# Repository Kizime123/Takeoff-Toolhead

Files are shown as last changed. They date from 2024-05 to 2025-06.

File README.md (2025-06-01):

# Takeoff-Toolhead-Clamps
Is it about time to *takeoff* your current toolhead? Well you're in the right spot!

The **ONLY** fully open source SLM voron toolhead

An SLM toolhead using 3628s and [Chube](https://chubehotend.com), with no X loss. There will be some Y loss (17mm~ from hitting the front door) unless you have a [clicky clacky door](https://github.com/tanaes/whopping_Voron_mods/tree/main/clickyclacky_door), a v2.4 that allows moving the bed back, or a 4040-based frame, such as DoomCube

> [!WARNING]  
> For tridents, you need to cut the front left and rear leadscrew, or use [these](https://www.printables.com/model/486638-voron-trident-z-steppers-spacers) (recommended), to avoid losing travel

> [!WARNING]  
> For those aiming for high belt tensions, a pretension tool is necessary since the mount uses clamping. I recommend using [this one](https://www.printables.com/model/1027579-sovol-sv08-belt-helper-for-x-carriage).

## Luke's Laboratory is [selling kits for takeoff!](https://lukeslabonline.com/products/takeoff-toolhead) I'll be getting a percentage of each sale. If you don't wanna wait/want to support me purchase from them!

## 3Dkatten is [selling kits for takeoff!](https://3dkatten.se/en/products/takeoff-toolhead) I'll be getting a percentage of each sale. If you don't wanna wait/want to support me purchase from them!

## Klipper Setup https://github.com/KalicoCrew/kalico Kalico is the recommendation for MPC

```
[beacon]
x_offset:-23.48

[fan] #only 2 wires
max_power: 1 #set to .8 for kraken (btt moment)
off_below: 0.13

[verify_heater extruder] #use with mpc
max_error: 120
check_gain_time: 25
hysteresis: 10

[extruder]
control = mpc
heater_power: 120
#ambient_temp_sensor: temperature_fan chamber #if you have a chamber thermistor
cooling_fan: fan
#Recommend 9 minimum FAN_BREAKPOINT for calibration

#Example MPC config from Ericzimmerman
# block_heat_capacity: 26.1100
# sensor_responsiveness: 0.115066
# ambient_transfer: 0.0708064
# fan_ambient_transfer: 0.0708064, 0.147823, 0.179016, 0.19074, 0.206899, 0.22524, 0.21861
```

## Extruders Compatiblity

<u>Option A Has mounts for:</u>

LGX Lite Pro

Vz-Hextrudort

Sherpa Mini (No K-face)

Sherpa Micro (With K-face), Mellow CNC Sherpa Micro supported, but no K-face is available

Orbiter 2/Peopoly Lancer Orbiter 2 Version

<u>Option B Has mounts for: </u>

Sherpa Mini (with K-face), Fysetc CNC Sherpa Mini supported 

Peopoly Lancer new/old (rotated COM for both)

DFA/Orbital Ascender (PENDING OA RELEASE)

A3DP FXD 

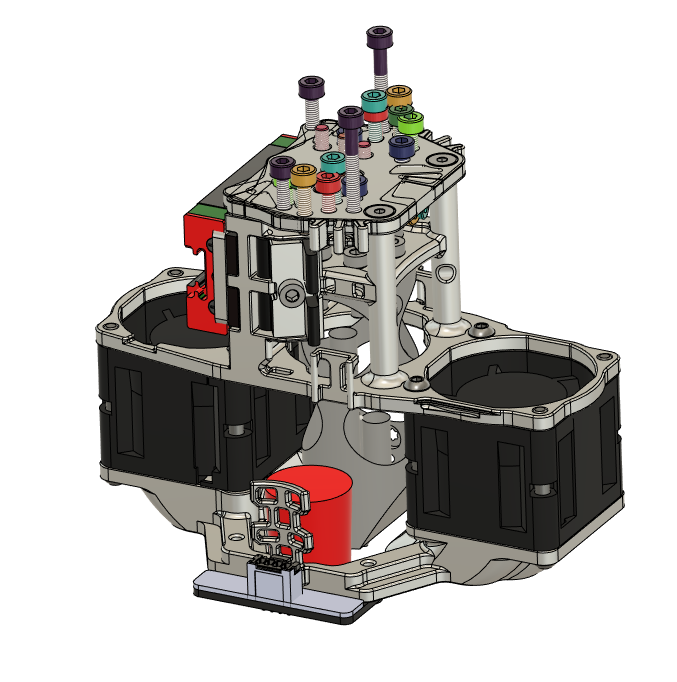
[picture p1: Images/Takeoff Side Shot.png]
Side View Image

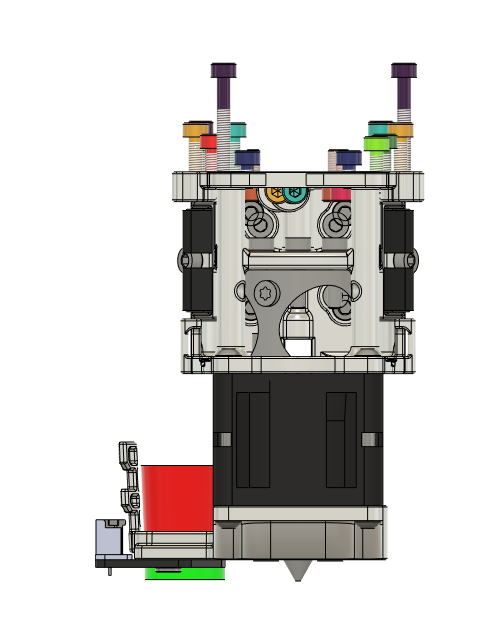
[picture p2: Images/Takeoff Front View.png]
Front View

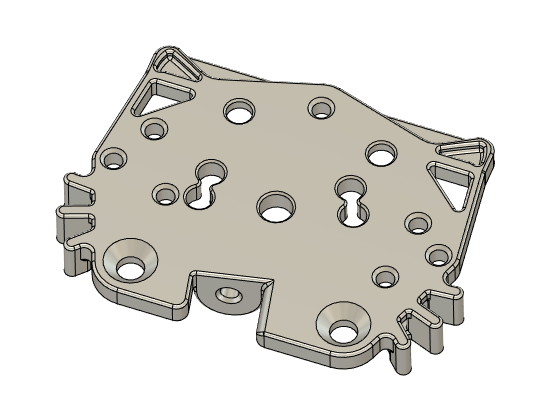
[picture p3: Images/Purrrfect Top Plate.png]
The Purrrfect Toolhead


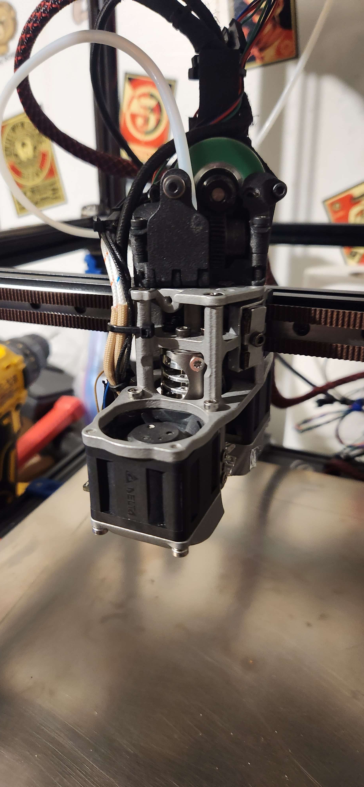
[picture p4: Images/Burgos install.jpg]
My Beautiful Toolhead installation


## How does that belt path work?
The belt path relies on you deflecting the belt with itself so that it's straight, the belt must be feed with another piece of belt (or itself) near the XY joints so it's parallel.

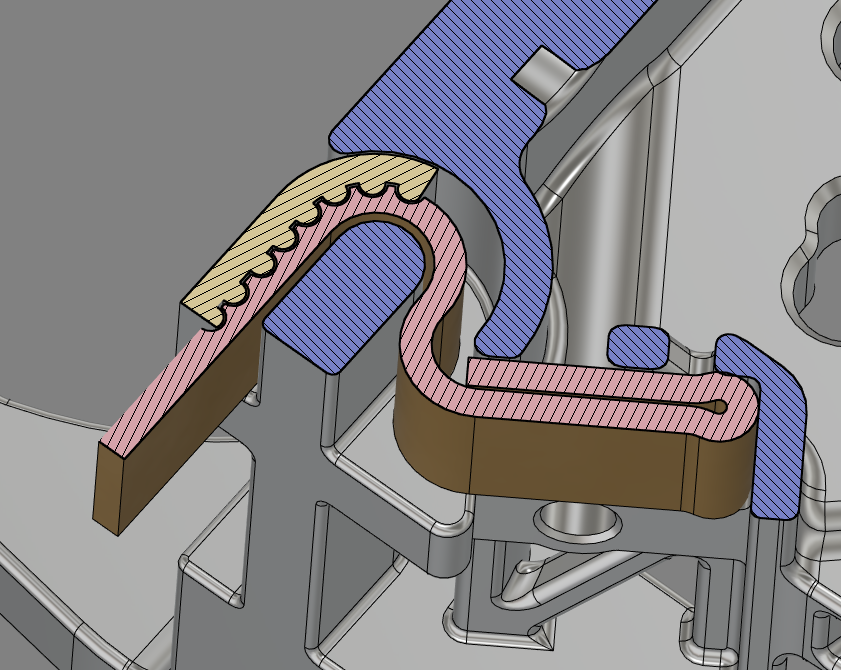
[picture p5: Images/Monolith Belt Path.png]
Monolith Belt Install

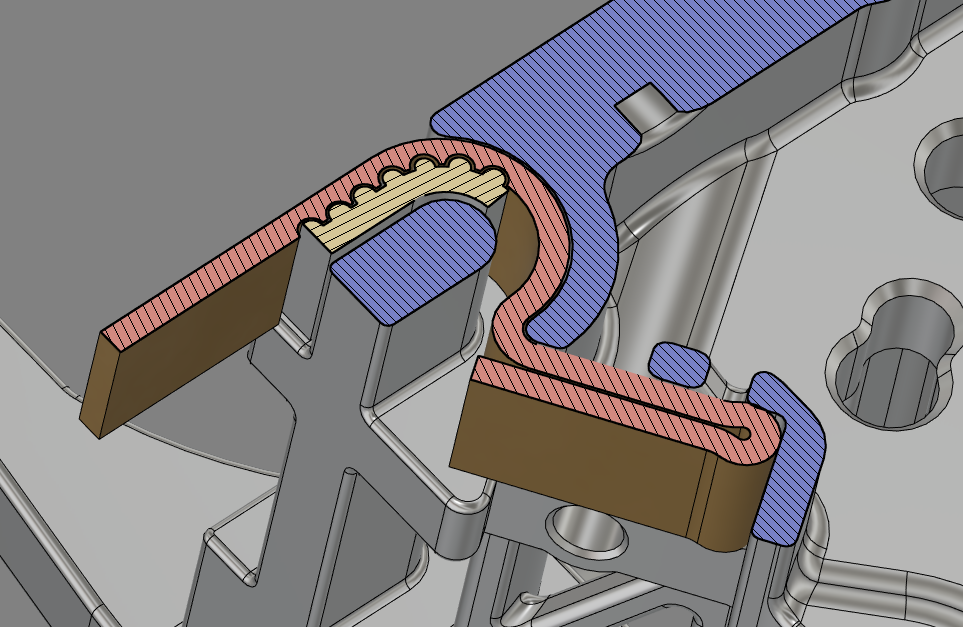
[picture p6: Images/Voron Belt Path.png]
Voron Belt Install


<a href='https://ko-fi.com/burgo' target='_blank'>Buy Me a Coffee at ko-fi.com</a> 

**Want help/ learn more: Join my discord!**

Join the Discord (https://discord.gg/6pRs2kgsKK)

### BIG Shoutout to Turtlecrawler for helping me redraw the mainbody, a clean timeline is always fun in the end.

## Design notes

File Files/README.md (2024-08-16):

# WARNING
** THE ASSEMBLY IS A f3z IT WILL DOWNLOAD MANY FILES PUT IT IN A FOLDER **

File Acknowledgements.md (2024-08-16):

Cbon for the initial K3 ducts which I've borrowed the geometry from for my ducting.

Tiger3dPrinting for his unparallel toolhead I was inspired by. [Tigers Instagram](https://www.instagram.com/tiger3dprinting/)

TurtleCrawler for  pushing me to make takeoff in its current state. Turtle helped alot with many ideas and redrew the mainbody, helped save me many hours of work.

[Cloakedwayne](https://github.com/CloakedWayne) for helping me figure out the currently belt path

Stacking for dealing with me in attempts at a manual lmao.

All the other people too who've bounced back ideas along the way with me/ helped me learn this much!

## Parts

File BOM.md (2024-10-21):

# BOM
This is the list of all the parts/tools you need to build this toolhead. **SHCS is ALWAYS the suggestion.**

## Luke's Laboratory is [selling kits for takeoff!](https://lukeslabonline.com/products/takeoff-toolhead) I'll be getting a percentage of each sale, if you don't wanna wait/ want to support me purchase from them!

## 3Dkatten is [selling kits for takeoff!](https://3dkatten.se/en/products/takeoff-toolhead) I'll be getting a percentage of each sale, if you don't wanna wait/ want to support me purchase from them!

## Parts and screws:
x1 Chube Air/Conduction (Goliath air is untested and unsure if will need a hotend fan)

x1 Beacon Rev H (SLM Ducts WILL NOT work with Rev D)

x2 Delta [3628 Fans](https://www.digikey.ca/en/products/detail/delta-electronics/FFB03612EHNYCL/6580720)

x1 SLM Mainbody

x1 SLM or Lazer Cut Top Plate

x2 Laser Cut Belt Clamps

x1 Duct SLM/FFF (FFF soon to come when not as burned out with the project)

x9 M3x35mm BHCS

x8 M3x12mm SHCS/BHCS

x2 M3x8mm FHCS

x2 M3x6mm ULP (BHCS also works, but this should come with your beacon)

Excess Gates belts to be used as a Spacer

### MGN9H Specific:
1x MGN9H 3mm Spacer (Accept unparrallel belts with a 1/8" spacer as an american or sand it down!)
x4 M3x8 SHCS/BHCS 

### MGN12H Specific:
x4 M3x6mm SHCS/BHCS (SHCS is just better don't @ me.)

### Extruder Specific:

There are two main top plates, A or B
** Laser cut plates DO NOT support k face extruders **

Option A Has mounts for:

LGX Lite Pro

Vz-Hextrudort

Sherpa mini (NO K FACE)

Sherpa Micro (With K Face). Mellows sherpa micro k face isn't supported as its not the stock length.

Orbiter 2/ Peopoly Lancer Orbiter 2 mount

Option B Has mounts for:
Sherpa Mini (with K face), Fysetc cnc Sherpa mini supported

Peopoly Lancer new/old (rotated COM for both)

DFA/ Orbiter Ascender (PENDING OA Release)

A3DP FXD 

Vz Hextrudort:

x1 Top Plate A

x2 M3x10mm SHCS/BHCS

Sherpa Micro:

x1 Top Plate A

x2 M3x12mm SHCS/BHCS

x1 M3x8mm SHCS/BHCS

Sherpa Mini:

x1 Top Plate B (For K face support)

x2 M3x12mm SHCS/BHCS

x1 M3x8mm SHCS/BHCS

DFA:

x1 Top Plate B

x2 M3x25mm SHCS/BHCS

x2 M3x10mm SHCS/BHCS

LGX Lite Pro:

x1 Top Plate A

x2 M3x8mm FHCS

x2 M3x6mm SHCS/BHCS

FXD:

x1 Top Plate B

x4 M3x5mm SHCS/BHCS

Orbiter v2:

x1 Top Plate A

x2 M3x8mm SHCS/BHCS

Peopoly Lancer:

x1 Top Plate B

x2 M3x8mm SHCS/BHCS

## Tools:
90 Degree countersink 

M3x.5mm Tap

2.5mm Drill bit

3.2mm or 1/8" Clearance drill bit (Probably unnecessary)

4mm Drill bit (For filament path)

Aluminum Foil Tape (For SLM Duct screw covers and fdm duct faces beside chube)

A file

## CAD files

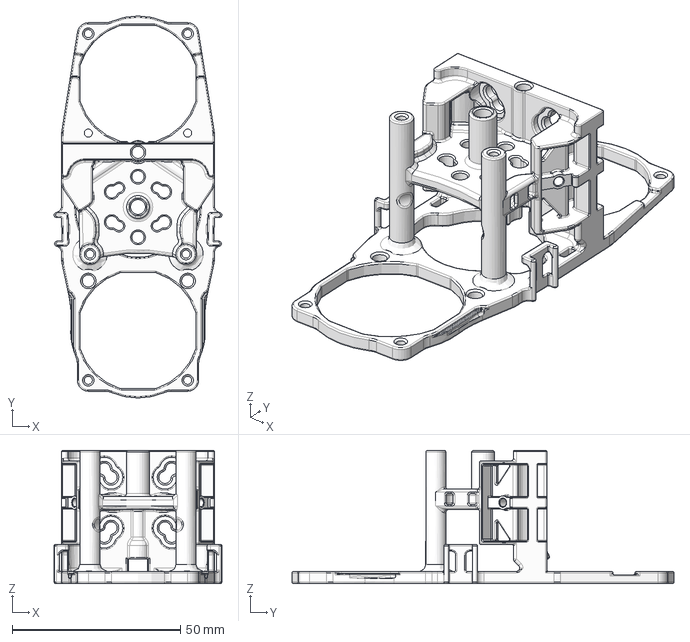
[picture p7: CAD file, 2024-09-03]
Files/SLM/Takeoff V2.1 Mainbody Redrawn By TurtleCrawler.step
49.9 x 113.4 x 39.5 mm

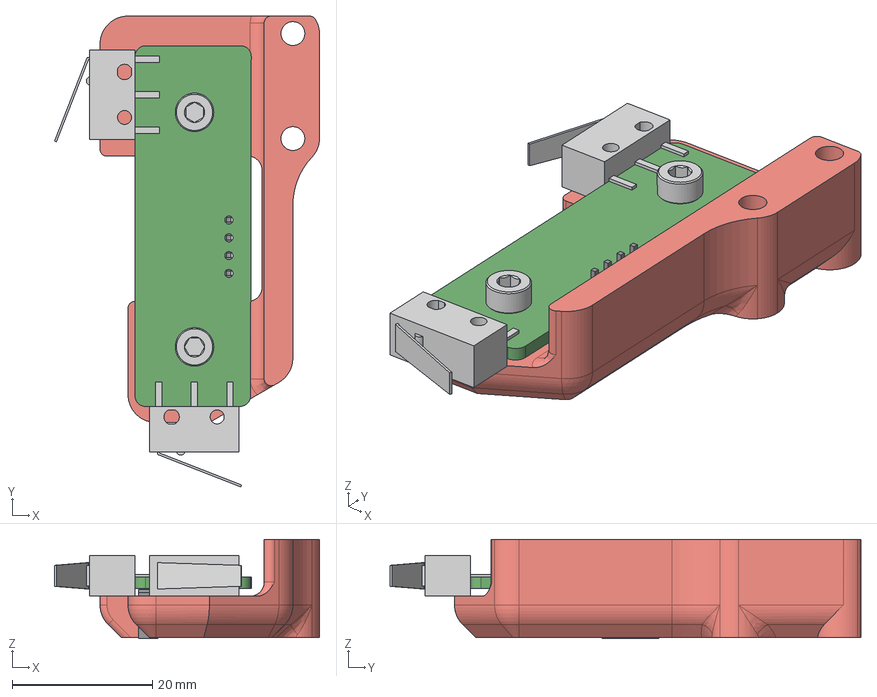
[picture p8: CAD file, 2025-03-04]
Endstop mods/D2F Endstop Pod Stock Voron Takeoff Edition.step
37.8 x 67.3 x 14.2 mm
M3x8 SHCS (1) (1) (1) x 2

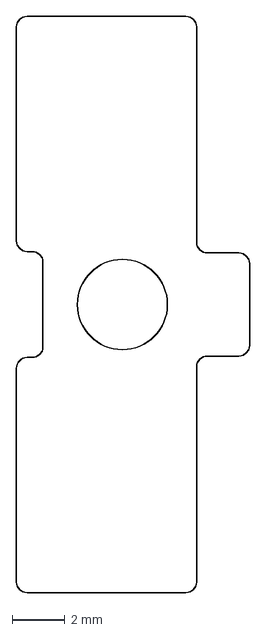
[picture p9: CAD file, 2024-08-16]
Files/Laser Cut/3-3.175mmx2 Belt Clamps.dxf
8.80 x 21.8 mm

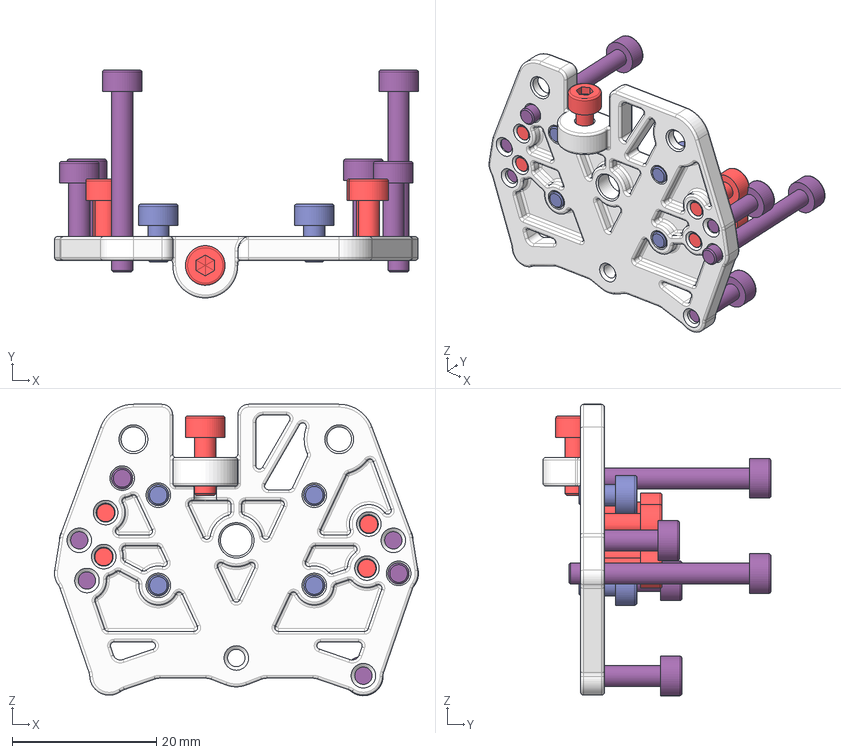
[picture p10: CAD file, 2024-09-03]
Files/Top Plates/Takeoff v2.1 Top Plate B.step
50.4 x 31.6 x 40.4 mm
Hexagon Socket Head Cap Screw ISO 4762 - M3 x 8 Steel 4.6 Plain v1 x 5
Hexagon Socket Head Cap Screw ISO 4762 - M3 x 25 Steel 4.6 Plain v1 x 2
Hexagon Socket Head Cap Screw ISO 4762 - M3 x 10 Steel 4.6 Plain v1 x 4
Hexagon Socket Head Cap Screw ISO 4762 - M3 x 5 Steel 4.6 Plain v1 x 4

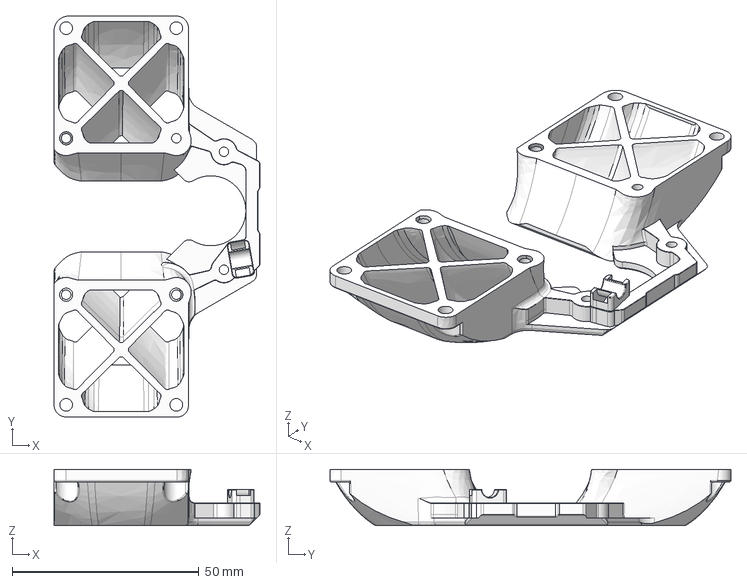
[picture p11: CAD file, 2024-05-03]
Step for SLM Order/Takeoff SLM Duct.step
55.2 x 107.4 x 15.0 mm

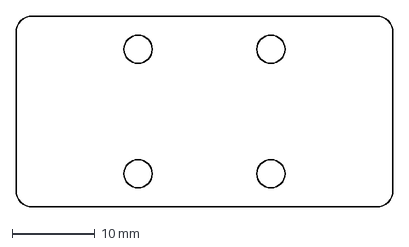
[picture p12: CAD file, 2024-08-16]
Files/Laser Cut/3mm MGN9H Spacer.dxf
45.4 x 23.0 mm

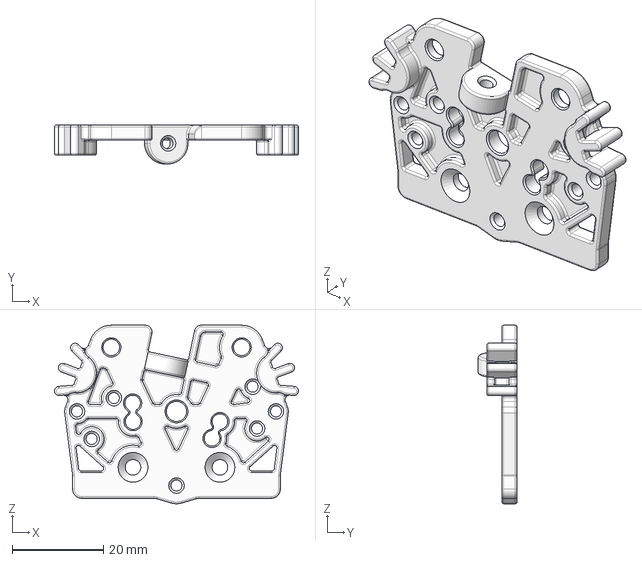
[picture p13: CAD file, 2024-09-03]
Files/Top Plates/Takeoff v2.1 Top Plate A Purrrfect Edition.step
53.3 x 8.50 x 39.0 mm

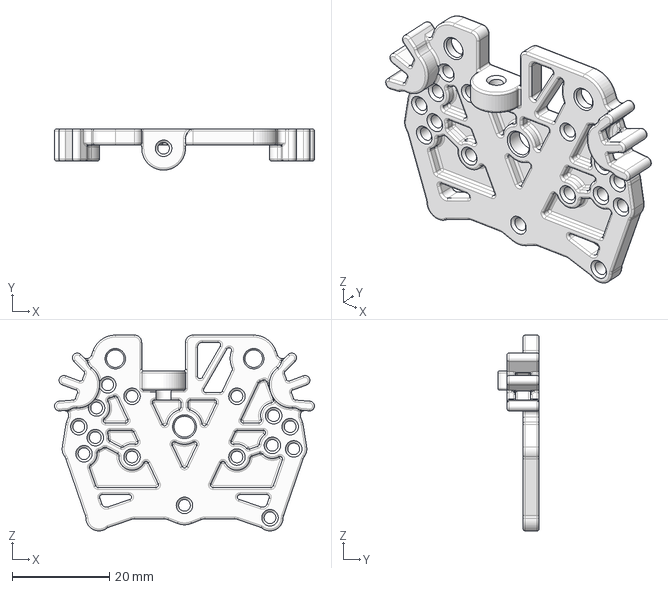
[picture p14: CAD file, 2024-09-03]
Files/Top Plates/Takeoff v2.1 Top Plate B Purrrfect Edition.step
53.5 x 8.50 x 40.3 mm

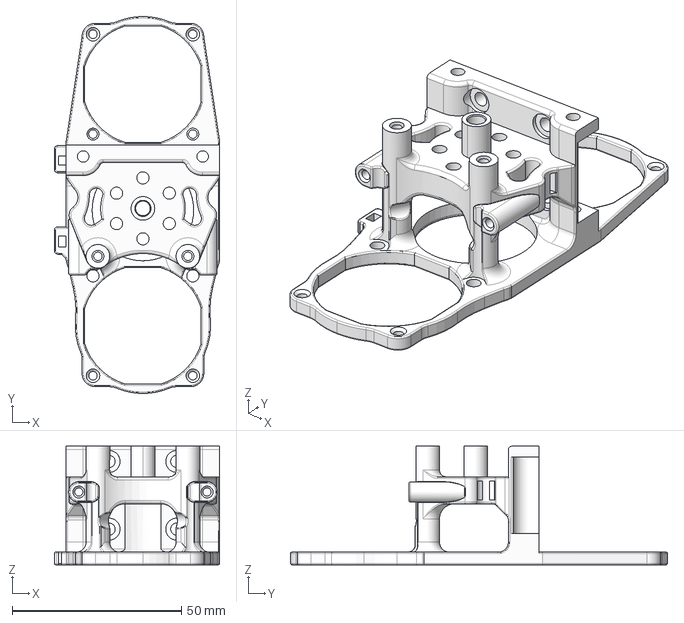
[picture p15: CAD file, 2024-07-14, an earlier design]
Deprecated/Takeoff Mainbody v5.step
48.9 x 111.4 x 35.0 mm

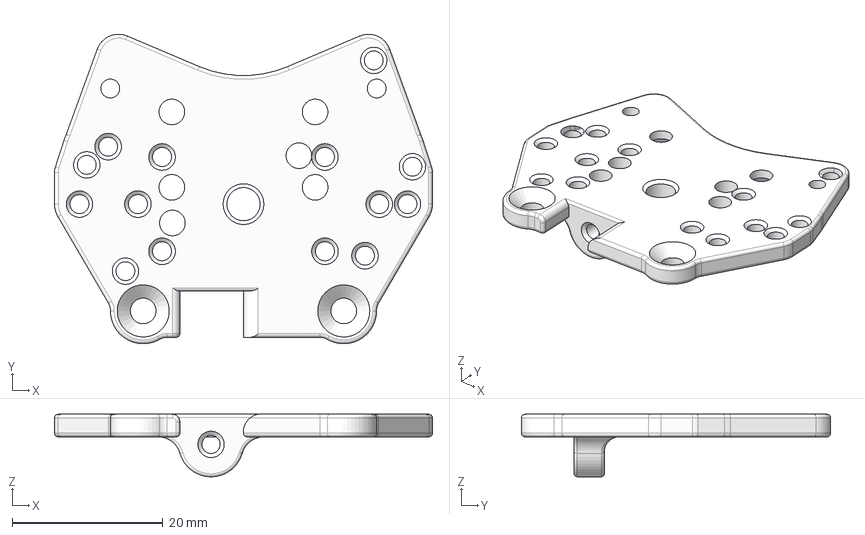
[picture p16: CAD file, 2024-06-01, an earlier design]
Deprecated/Takeoff SLM Top Plate v3.step
50.1 x 41.0 x 8.29 mm

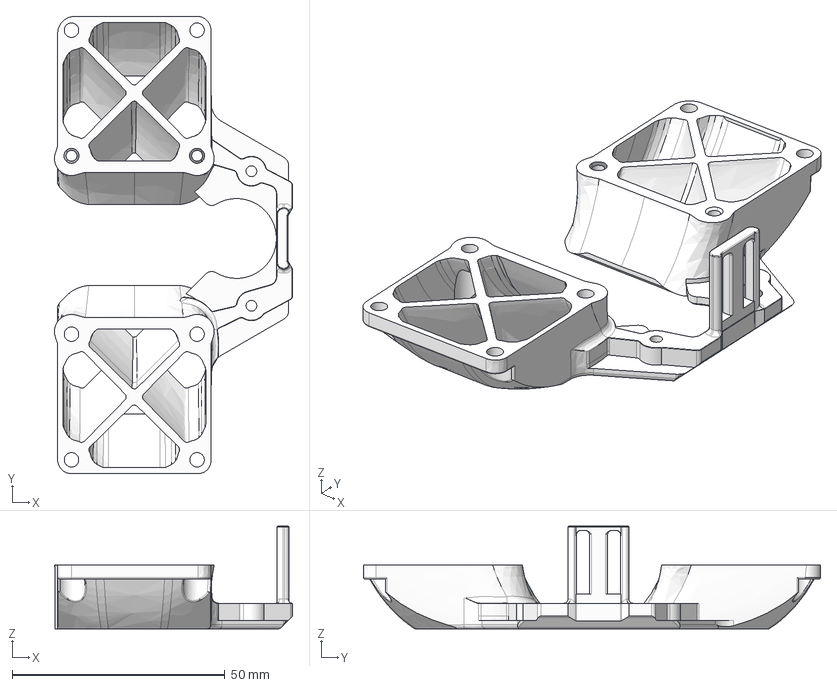
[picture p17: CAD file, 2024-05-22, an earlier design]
Deprecated/Takeoff SLM Duct v3.step
55.9 x 107.4 x 24.1 mm

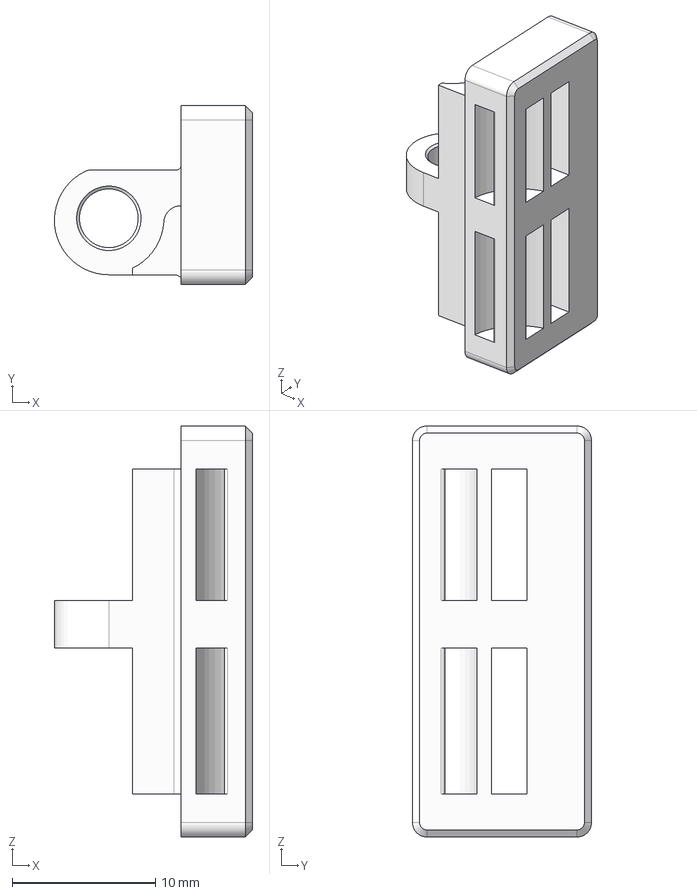
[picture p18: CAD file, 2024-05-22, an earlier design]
Deprecated/Takeoff SLM Belt Clip x2 v3.step
13.8 x 12.5 x 28.7 mm

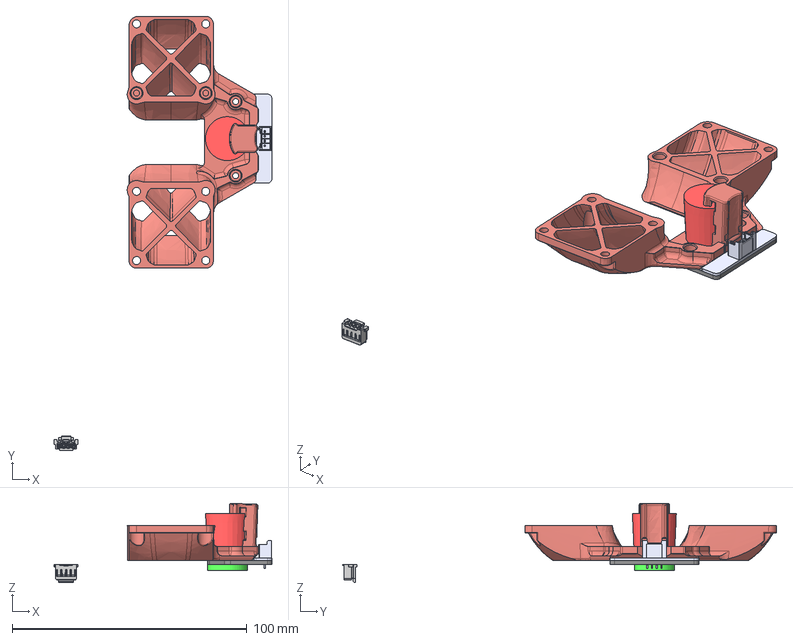
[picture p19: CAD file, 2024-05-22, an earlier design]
Deprecated/Takeoff FDM Duct Rev 2 .step
93.0 x 185.2 x 33.8 mm
Optimal Spacing
PCB
ELECTRONICS ZONE
Top Keep Out ZONE
Beacon Sherlock

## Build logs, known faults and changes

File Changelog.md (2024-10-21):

Changelog:
2024-05-22 
SHCS for the rail mounting didn't fit; I hadn't realized this earlier because it's a factor that changed from when I was using tiger3dprintings cad as a base for my changes.
Belt clips need an increase in tolerance for the excess belt section.
Change the back screws to all be bottom mounted, So the duct can be installed after going onto the linear rail. As a result, Aluminum foil tape has been added to the BOM + will be used to cover the screw holes.
Beacon Sherlock gave more clearance + better strain relief (SLM Duct Changes)
Rail mounting screws were changed to M3x8mm SHCS

BOM Changes
4x M3x8mm SHCS (added)
4x M3X10mm SHCS (removed)
Aluminum Foil for ducts (added)

Have an older version of takeoff. What parts are reusable?
The Mainbody + Duct are the only parts that are not reusable with the current changes. I initially decided that for better airflow characteristics, the maintenance far outweighs the cons when you use aluminum foil to cover those sections.

2024-06-01
Add support for orbiter v2

2024-08-15
# Takeoff V2!
So much has changed now, I don't quite know where to start. Belt Clips have been ditched, instead I designed a monolith and voron belt path! The idea being that you feed the belt thru the belt path twice so that it exits beside itself. It's feed beside a circular SLM feature so that the belts are parrallel and able to clamp without a custom option for monolith!

I added support for MGN9H with a spacer, I'll still live by mgn12h since the toolhead is heavy, extra support is always recommended with extra heft!

Reduced the thickness of the chube mounting surface from 6mm ish to 3.4mm

Added way more ziptie slots

Made the top plate two main options, A or B

Added the stylish Purrfectttt Options for A or B

Added a laser cut top plate for those who don't use a sherpa K face

Added holes for dragon pattern hotends

Many of the geometry has changed so I won't be noting it all down. Most of the changes occured in my discord

BOM Changes

Bye bye clip specific hardware!

x2 4mm OD x 3mm ID x 22.5mm L Steel tubes (removed)

x2 SLM Printed Belt Clips (removed)

1 less M3x35mm (removed)
M3x35mm Switched to BHCS focused due to the duct

x2 Laser Cut Belt Clamps  (added)

x4 M3x8mm SHCS/BHCS (removed)

x2 M3x10mm FHCS (removed)
x2 M3x8mm FHCS (added)

MGN9H Specific:

1x MGN9H 3mm Spacer (Accept unparrallel belts with a 1/8" spacer as an american or sand it down!) (added)

x4 M3x8 SHCS/BHCS (added)

MGN12H Specific:

x4 M3x6mm SHCS/BHCS (SHCS is just better don't @ me.) (added)

Chube: x6 M3x16mm SHCS/BHCS (removed)
x6 M3x12mm SHCS/BHCS (added)

2024-09-03
V2.1 

This update was alot smaller, I had parts come in from in3dtec that had worked but could use a bit more tolerancing. 

Ziptie slots had width tolerances changed from 2.8mm to 3.3mm (chube wire holes)/ 3.1mm (in whiskers) 

The bowden tube hole was changed from 4.3mm to 4.4mm as it was a bit too snug 

The radius before belts exit was changed from .5mm - 1mm 

2024-10-21

This update adds cad for goliath air fdm ducts, chube fdm ducts, a watercooled mainbody and updates the top plate A for 1 which doesn't have extra holes mean't for a change that I reversed. (Was going to have the top plate mountable from top or bottom but didn't fit well)

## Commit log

2024-04-04 Update Jaguar Toolhead Assembly.step
2024-04-22 QOL Changes
    Moved DFA 5deg less to allow for Countersunk top screws
    Modified the length for LGX lite pro screws (I have 1 now so can tell the lgx lite pro model sucks)
    Removed huvud compatibility as the screw holes would interfere with front duct.
    Made the cable management sections larger for accomodating larger wires such as the Lukelabs heater wires.
    Added a early FDM duct.
    Fixed an intersection with the lgx lite pro front screw and the sherpa micro standoff.
    [Jaguar Main Body.step, Jaguar SLM TOP PLATE.step]
2024-04-22 Fix Vz-Hex
    Same issue as lgx lite pro...
    [Jaguar Main Body.step, Jaguar SLM TOP PLATE.step]
2024-05-02 Reduce Weight + Add tolerances
    Reduced weight all over the place based on input shaper results.
    Added support for FXD (Screw length unknown)
    [Jaguar Main Body.step, Jaguar SLM Duct.step, Jaguar SLM TOP PLATE.step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]
2024-05-02 Update BOM.md
    Added FXD Screw Length
2024-05-03 Update Jaguar SLM Duct.step
    Add more clerances for extruders
    [Jaguar SLM Duct.step]
2024-05-10 Rename to Takeoff
    RIP Takeoff my bent sheetmetal toolhead, however I couldn't stand jaguar as a name.
    [Jaguar SLM Belt Clip x2.step, Takeoff Main Body.step, Takeoff SLM Belt Clip x2.step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]
2024-05-15 Update Takeoff Toolhead Assembly.step
2024-05-22 add changed files.
    Github was being stupid
    [Takeoff FDM Duct Rev 2 .step, Takeoff Main Body Rev 4.step, Takeoff Main Body.step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]
2024-05-22 fix import issue
    [Takeoff SLM Duct v2.step, Takeoff SLM Duct v3.step]
2024-05-29 add the atributes for my toolhead
2024-06-01 Add support for orbiter v2 + cleanup names
    added more holes to the top plate. These with a purpose aka orbiter v2.
    [Takeoff Main Body Rev 4.step, Takeoff Main Body v4.step, Takeoff SLM Belt Clip x2 rev 3.step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]
2024-07-14 Fix Hole errors
    fix mounting surface error and holes
    [Takeoff Main Body v4.step, Takeoff Mainbody v5.step]
2024-08-16 TAKEOFF V2 WOOOOO
    CLAMPS CLAMPS AND WELL CLAMPS!!!!
    [3mm MGN9H Spacer.dxf, Takeoff FDM Duct Rev 2 .step, Takeoff Mainbody v5.step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]
2024-08-16 I forgor lasers melty too close
    [Takeoff v2 Top Plate A Laser Cut.dxf, Takeoff v2 Top Plate B Laser Cut.dxf]
2024-08-16 Found a missing Fillet
    Also step files > stl yolo
    [3-3.175mmx2 Belt Clamps.dxf, Takeoff v2 Mainbody Redrawn By TurtleCrawler.step, Takeoff v2 Top Plate A Purrrfect Edition.step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]
2024-08-18 Fix some holes in the ducts tolerances
    Some holes were modelled at 3.7mm and some 3.4mm where 3.6mm should be done to be bout 3.3mm irl
2024-08-21 Update BOM.md
    Fix formating
2024-09-03 Update to rev 2.1
    View the changelog for a breakdown
    [Takeoff V2.1 Mainbody Redrawn By TurtleCrawler.step, Takeoff v2 Mainbody Redrawn By TurtleCrawler.step, Takeoff v2 Top Plate A Purrrfect Edition.step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]
2024-10-10 add fdm chube duct
2024-10-10 Update Takeoff V2 FDM Ducts v1.stl
2024-10-21 stuff i guess (#2)
    * Update README.md
    * Update README.md
    Uhhh
    * Update README.md
    * Update README.md
    * Update README.md
    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
2024-10-21 Update top plate A + assembly for new files
    [Takeoff v2.1 Top Plates A.step]
2025-03-04 add Monolith X Endstop to stop caza blocking me
2025-03-04 Create D2F Endstop Pod Stock Voron Takeoff Edition.step
    [D2F Endstop Pod Stock Voron Takeoff Edition.step]
2025-05-05 add klipper section
2025-05-15 add x endstop + wc cad
